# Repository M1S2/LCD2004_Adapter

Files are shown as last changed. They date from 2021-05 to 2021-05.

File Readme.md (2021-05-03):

# LCD2004 Adapter

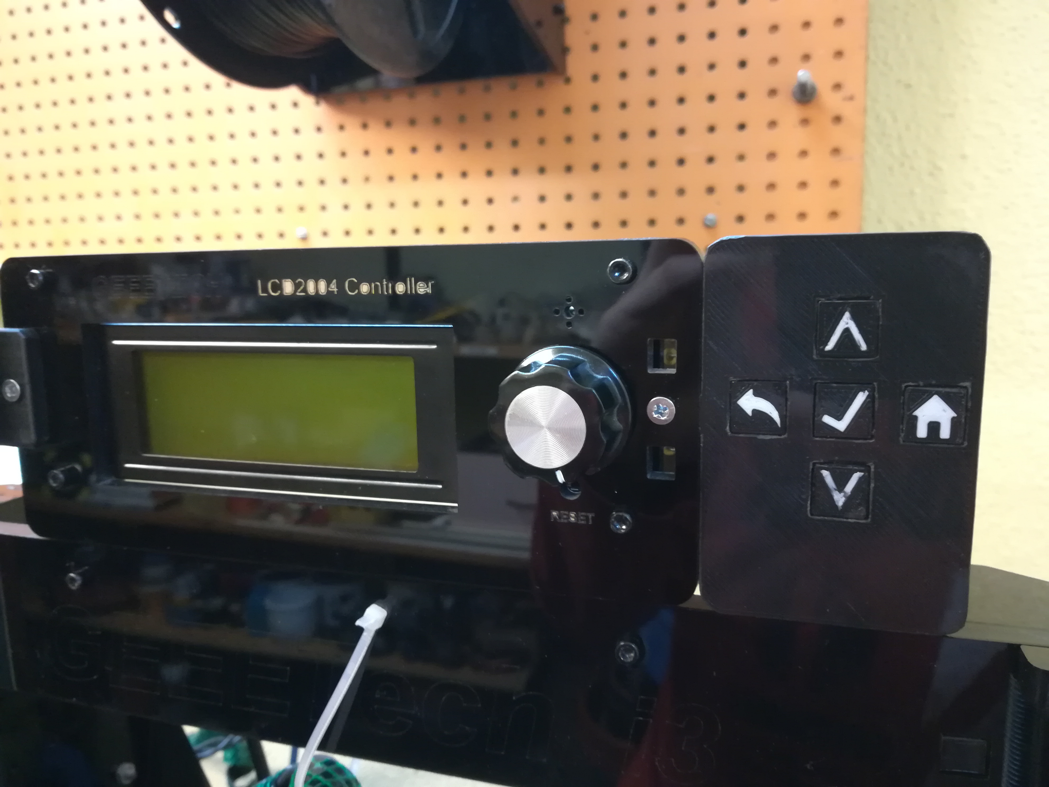
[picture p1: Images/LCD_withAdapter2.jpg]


This is an adapter to connect the DZ2004A-V1.0 LCD (Geeetech Prusa i3 pro B display) to the BIGTREETECH SKR E3 DIP V1.1 main board (LCD port).
This adapter is necessary because:
- The wiring of the LCD connectors on the display and the main board are different. The LCD2004 adapter connects the correct traces to make the display work again.
- The encoder isn't used anymore. The LCD2004 adapter is adding 5 push buttons as replacement for the encoder. The principle is inspired by the Zonestar LCD. 

Limitations:
- The encoder is out of service. This isn't a big deal, because it wasn't used that often because Octoprint is used most of the time to control the printer. So the 5 button keypad seemed to be good enough. Refer to section "Using the encoder again" of this Readme for some links how the encoder can maybe be used again.

## Principle of the 5 button keypad
The LCD2004 adapter is using 5 buttons to control the printers functions. This is inspired by the Zonestar display. 
Depending on which button is pressed, a different voltage is generated at the ADC_KEYPAD pin. This pin is read by an ADC on the main board.
The "UP" button is located on the bottom side of the PCB. This is correct because up means scrolling up which is the button on the bottom.

**Caution:** The SKR E3 DIP main board (and many other 32-bit boards) are working on 3.3V logic. Most pins on the ARM Cortex M3 STM32F103RCT6 are 5V tolerant (you can connect 5V to them) **but the ADC pin isn't (don't connect 5V to it)**! The LCD2004_Adapter uses a 3.3V zener diode to produce the correct voltage.

## PCB
The schematic and PCB was created using EAGLE. It was designed to be manufactured using toner transfer method so all traces are as big as possible.

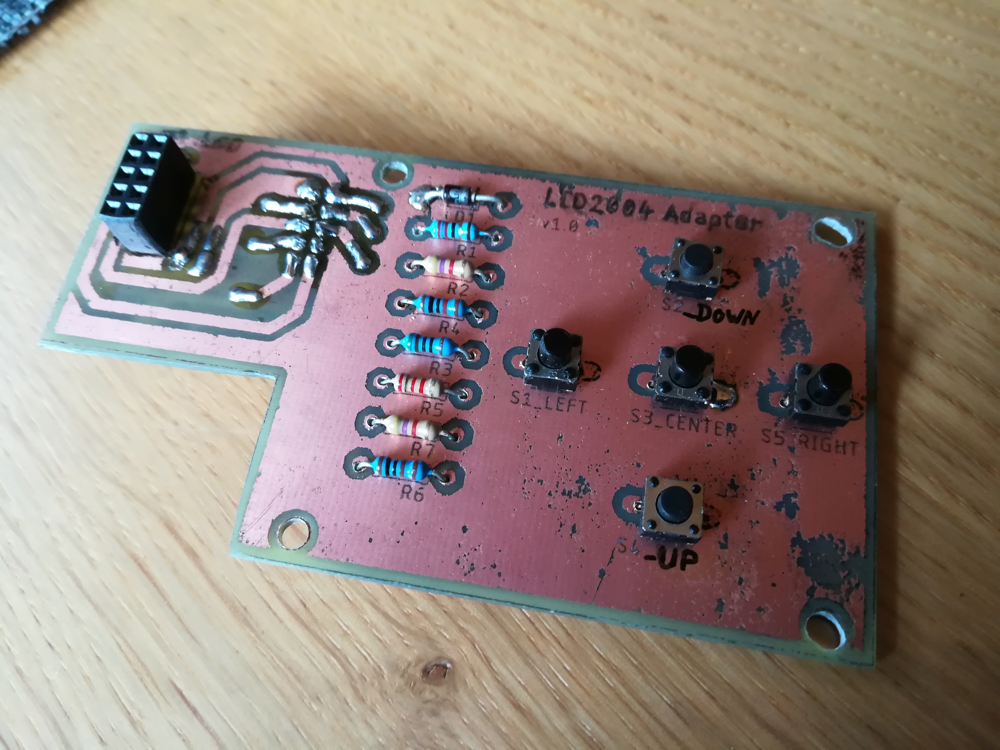
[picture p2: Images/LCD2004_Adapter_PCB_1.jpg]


## Housing
Print the following parts:
- 1x Keys_Housing.stl
- 1x Key_Back.stl and Key_Back_Icon.stl in one part
- 1x Key_Enter.stl and Key_Enter_Icon.stl in one part
- 1x Key_Home.stl and Key_Home_Icon.stl in one part
- 2x Key_Up_Down.stl and Key_Up_Down_Icon.stl in one part

**Caution:** The back, enter and home buttons are each 2 mm shorter because 2mm longer buttons were used here. The up and down buttons have the "correct" length.

The following parts are needed additionally:
- 2x 12mm spacers
- 1x M3 screw 10mm & M3 nut
- 2x wood screws 10mm

## Cabling
A default 10-pin ribbon cable can be used to connect the adapter with the main board. 
The only thing that must be changed here is to extract pin 8 (ADC_KEYPAD) on the main board side of the cable and wire it to the Servo pin (PA1) on the SKR E3 DIP board.

Cable complete                                |  SKR E3 DIP side
:--------------------------------------------:|:-------------------------:
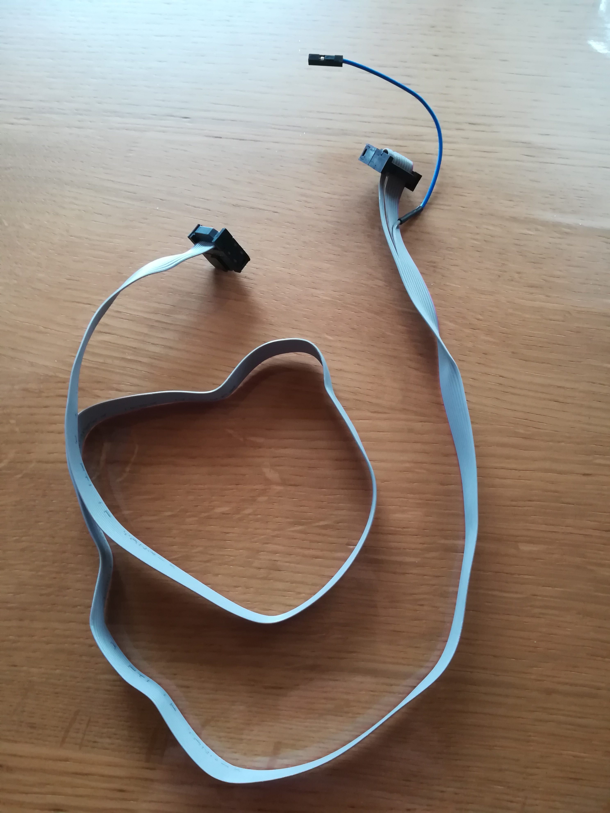
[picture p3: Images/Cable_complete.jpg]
Cable complete
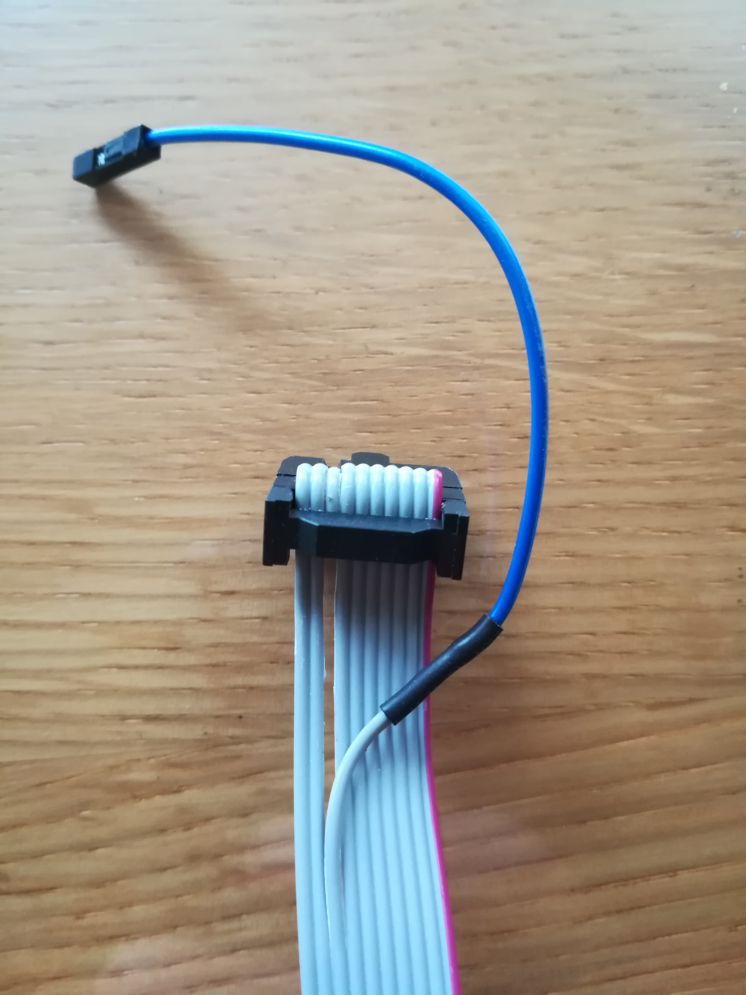
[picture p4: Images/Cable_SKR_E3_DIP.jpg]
Cable SKR E3 DIP side
 |  

## Firmware adaptions
Make the following adaptions to the Marlin firmware (line numbers are refering to Marlin 2.0.8):
- <Marlin root>/Marlin/Configuration.h: 
  Uncomment the `#define ZONESTAR_LCD` (in line 2086)
- <Marlin root>/Marlin/src/pins/stm32f1/pins_BTT_SKR_E3_DIP.h:
  Comment the line 190: `#error "CAUTION! ZONESTAR_LCD requires wiring modifications. See 'pins_BTT_SKR_MINI_E3_common.h' for details. Comment out this line to continue."`

## More Images
More images can be found in the [Images](/Images/) folder.

## Using the encoder again
To use the encoder again instead of the 5 buttons, here are some inspirations. Because Octoprint is used most of the time, there wasn't spent much time on this.

https://electronics.stackexchange.com/questions/231803/rotary-encoder-to-2-buttons

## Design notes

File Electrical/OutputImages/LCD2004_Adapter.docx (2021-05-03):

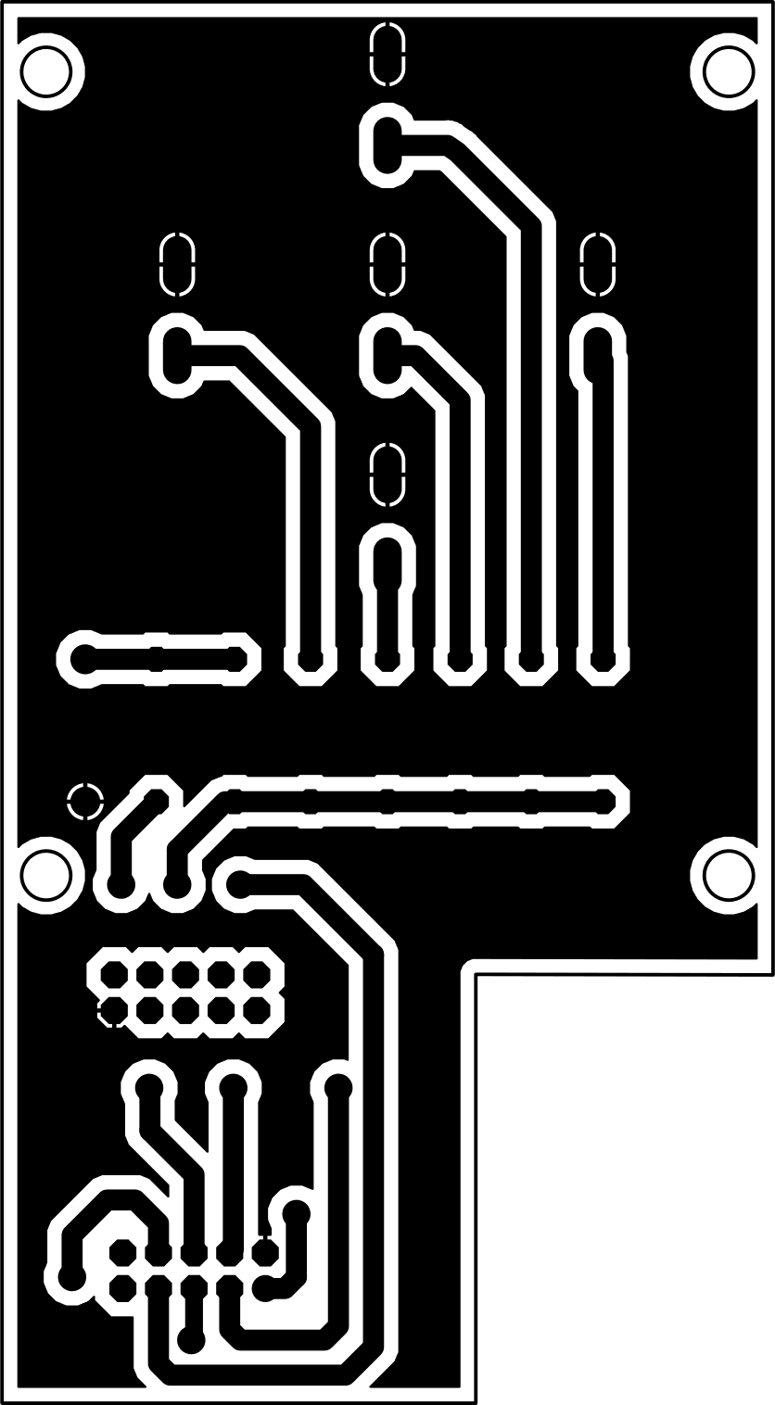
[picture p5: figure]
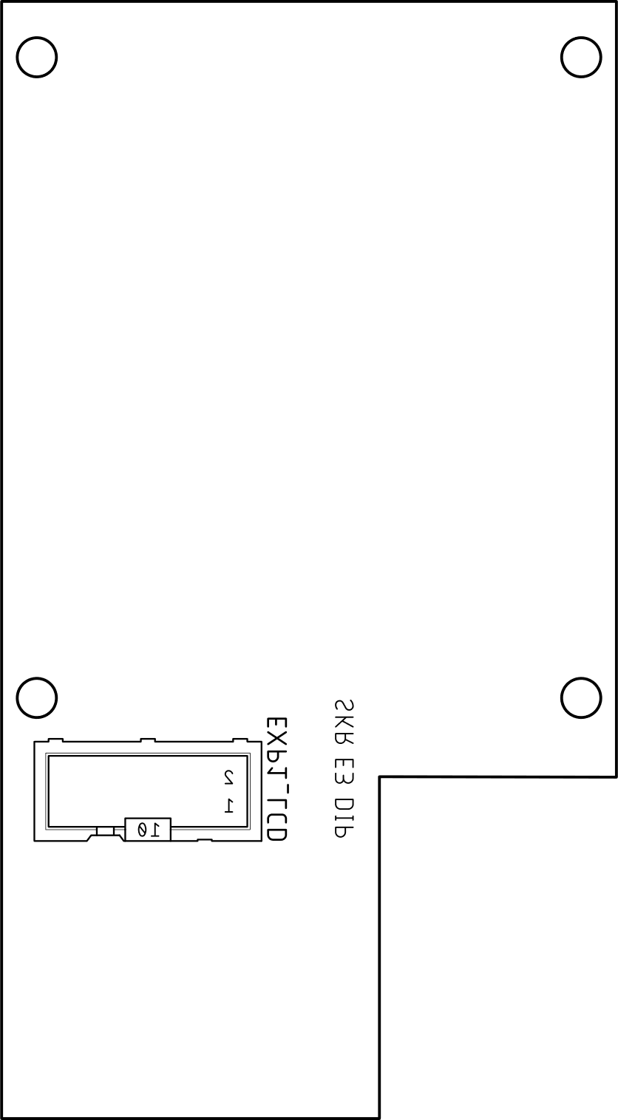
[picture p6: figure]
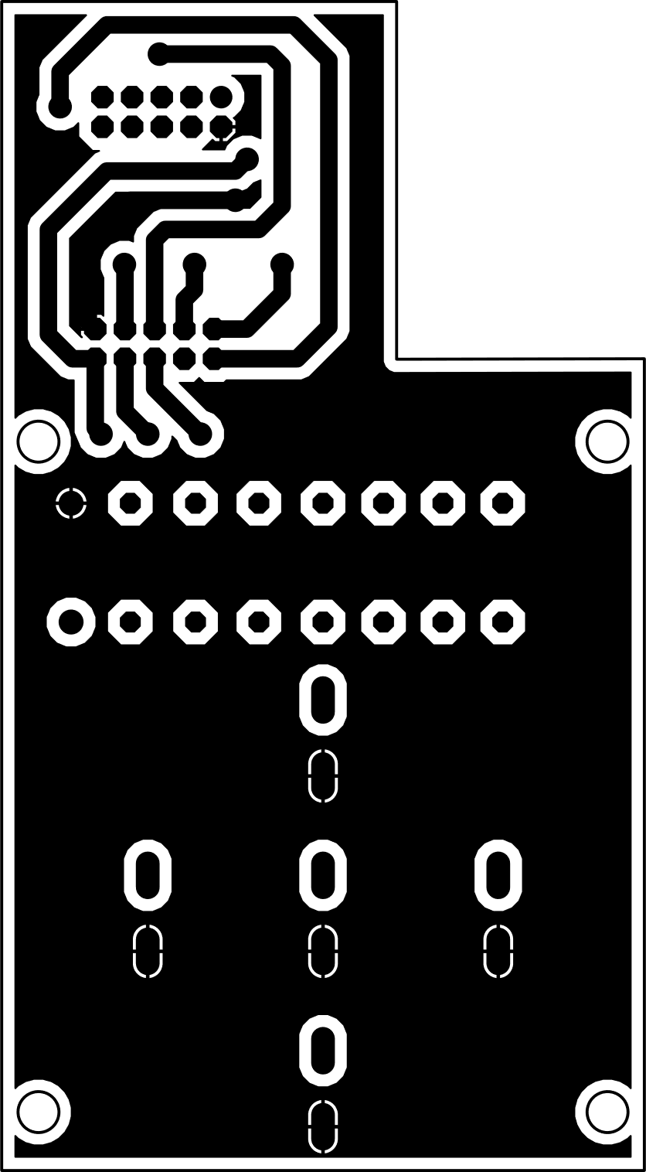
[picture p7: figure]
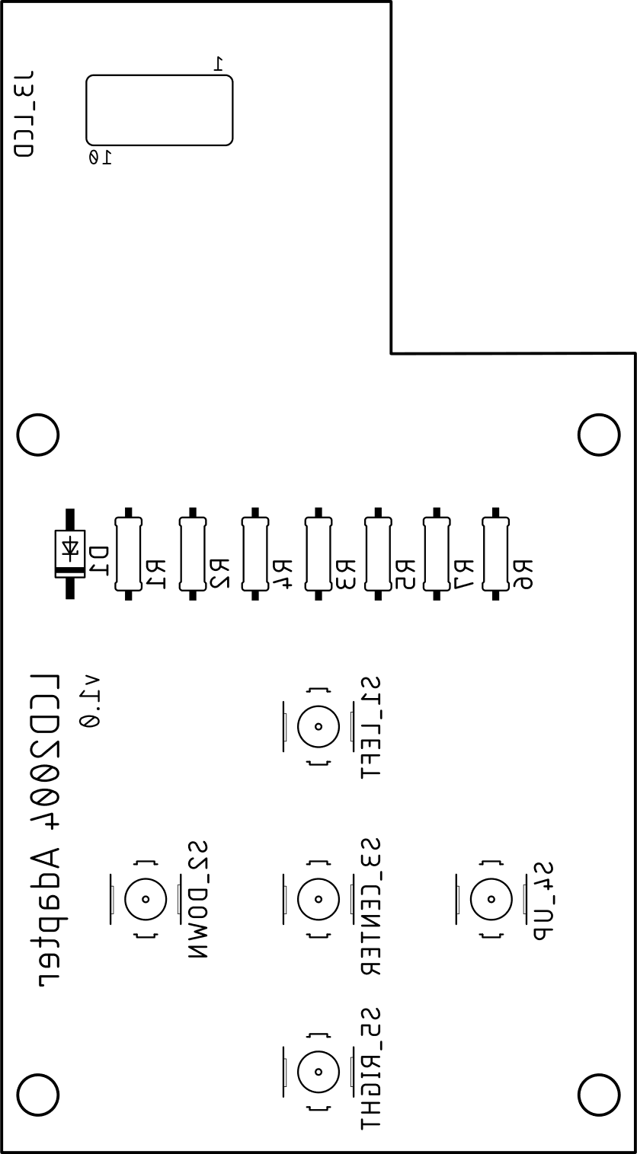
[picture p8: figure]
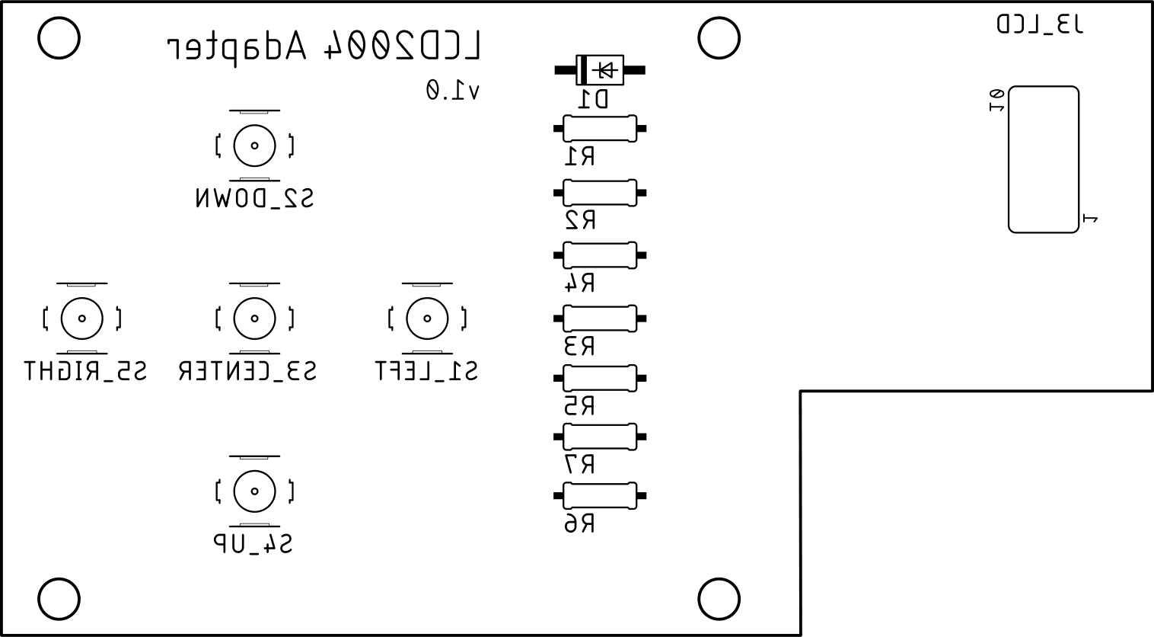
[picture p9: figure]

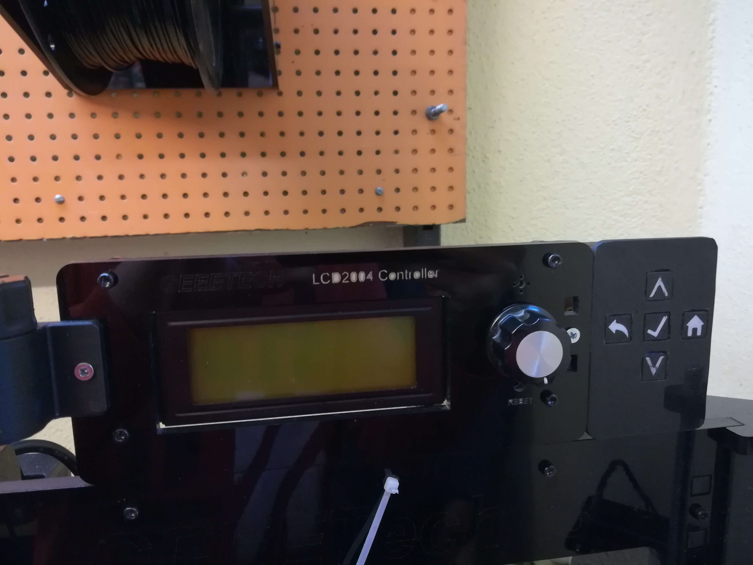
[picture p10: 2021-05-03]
Images/LCD_withAdapter1.jpg

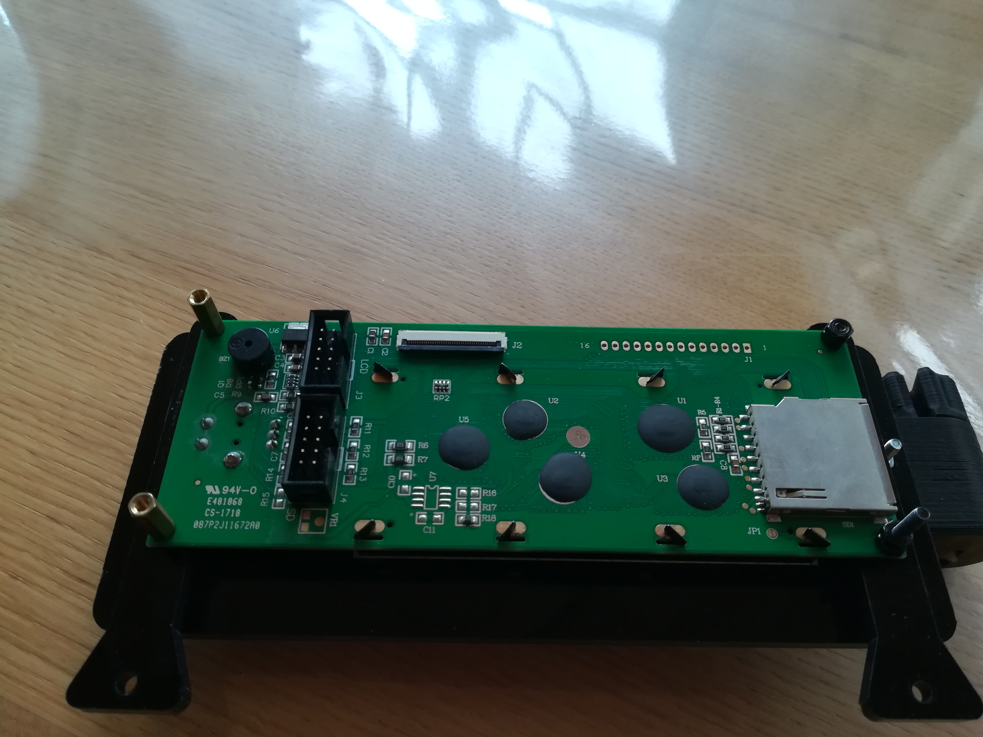
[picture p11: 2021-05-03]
Images/LCD_Back.jpg

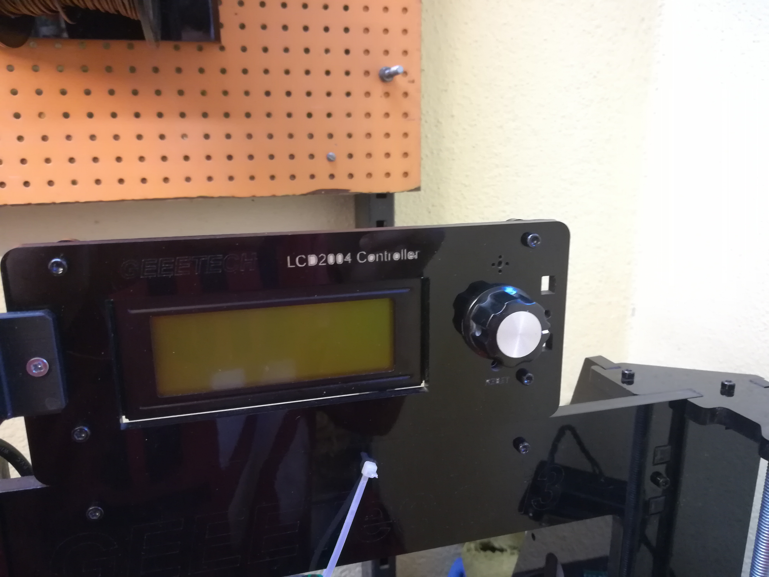
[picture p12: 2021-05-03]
Images/LCD_Before2.jpg

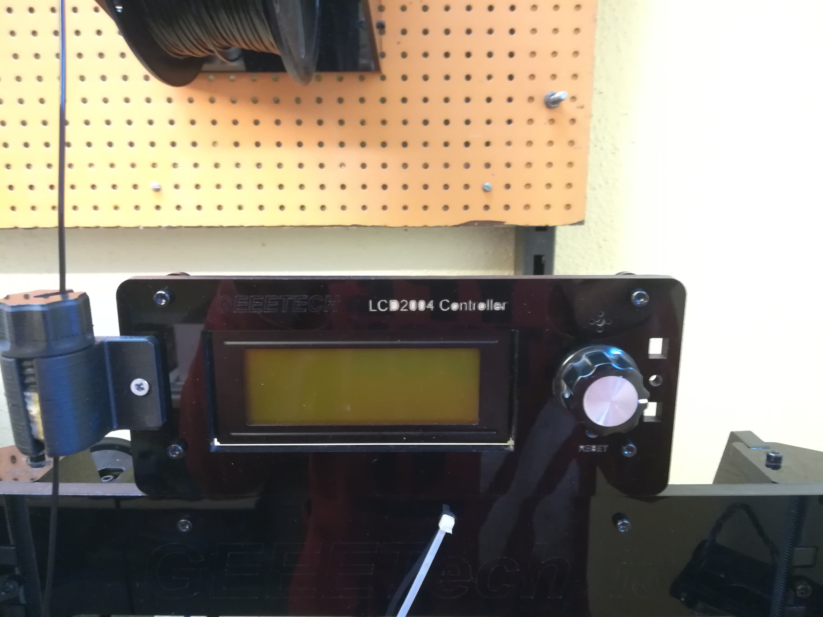
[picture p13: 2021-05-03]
Images/LCD_Before1.jpg

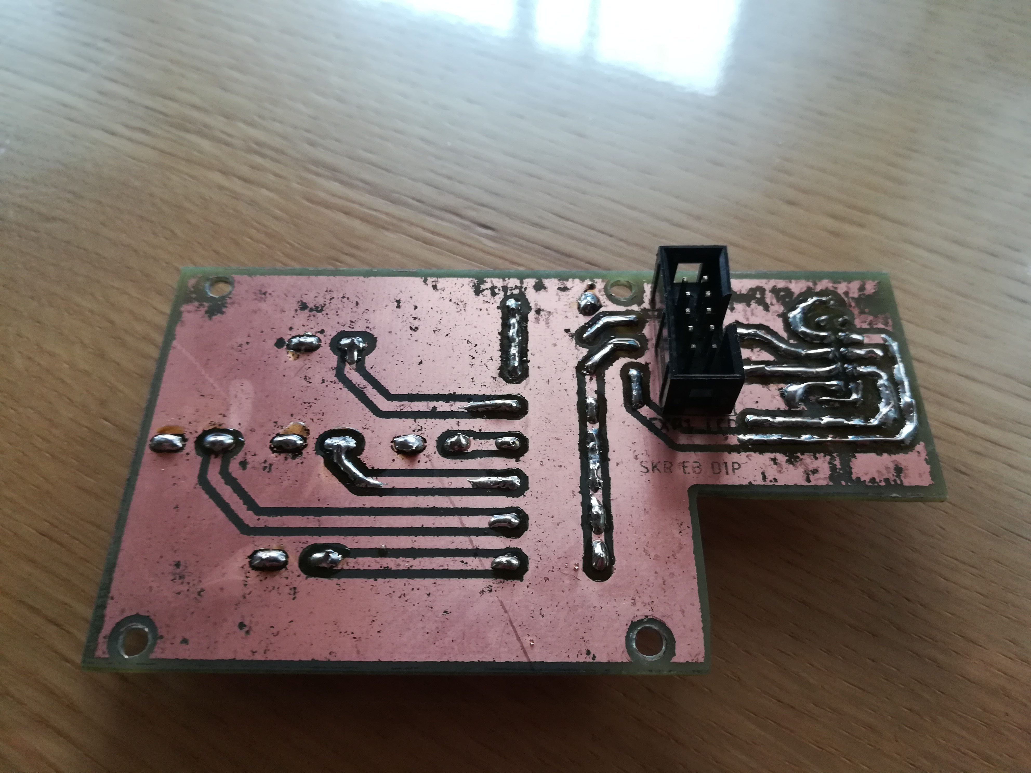
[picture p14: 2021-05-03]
Images/LCD2004_Adapter_PCB_2.jpg

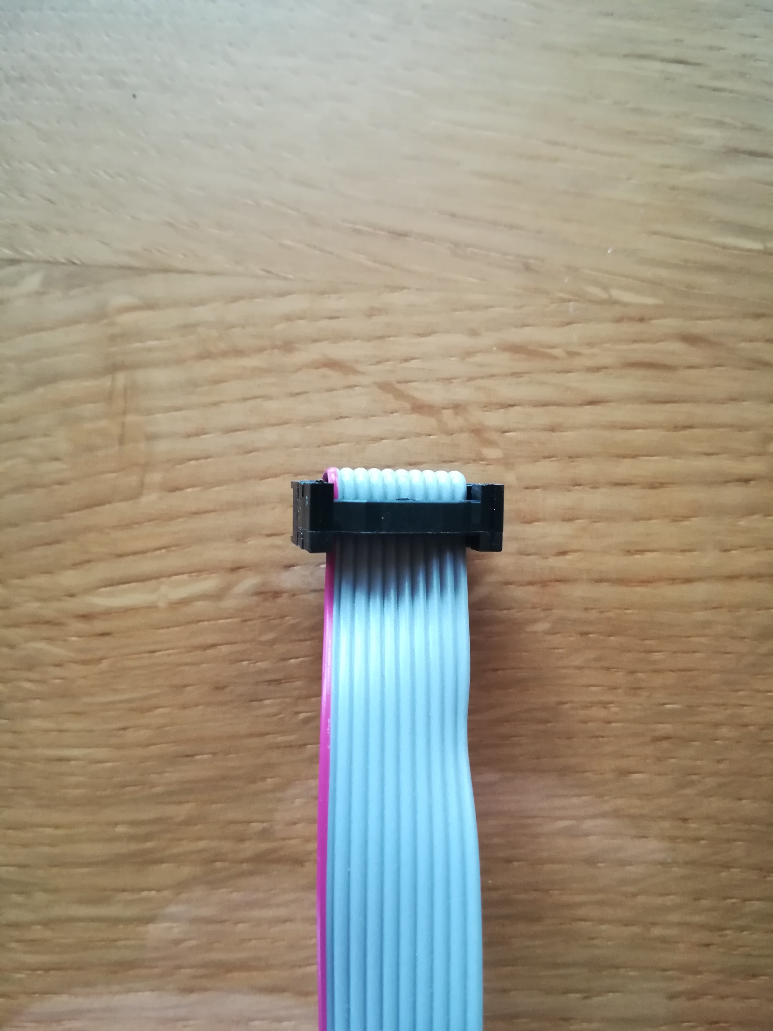
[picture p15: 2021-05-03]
Images/Cable_LCD2004_Adapter.jpg

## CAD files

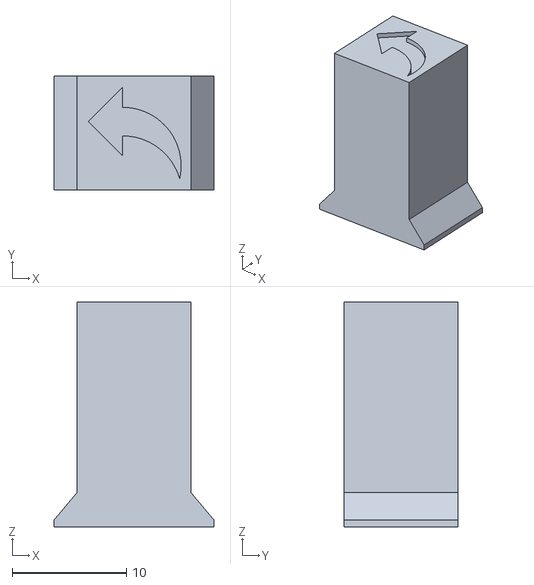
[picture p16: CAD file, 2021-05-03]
Mechanical/Key_Back.stl
14.0 x 10.0 x 19.7

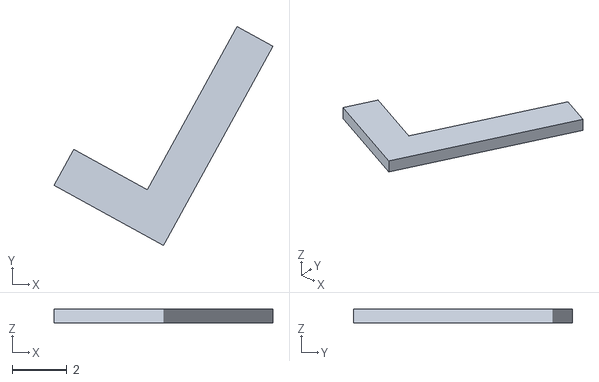
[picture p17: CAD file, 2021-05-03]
Mechanical/Key_Enter_Icon.stl
8.00 x 8.00 x 0.5

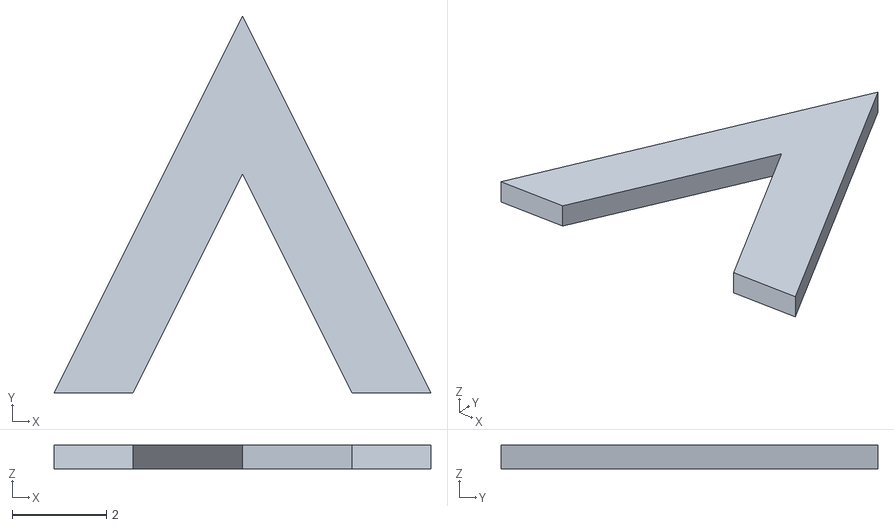
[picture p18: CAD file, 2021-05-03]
Mechanical/Key_Up_Down_Icon.stl
8.00 x 8.00 x 0.5

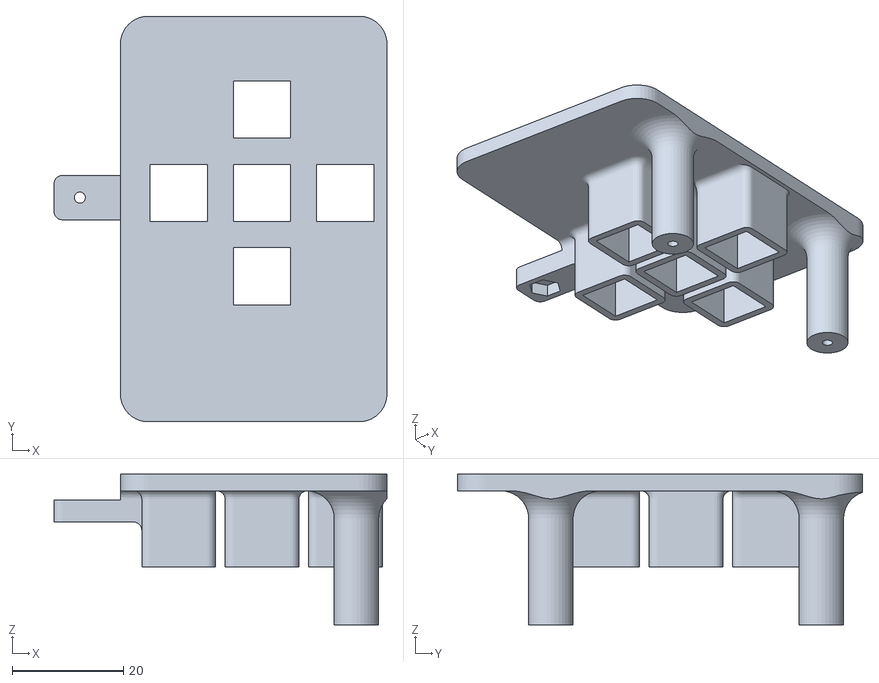
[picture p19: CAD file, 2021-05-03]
Mechanical/Keys_Housing.stl
60.0 x 73.0 x 27.1

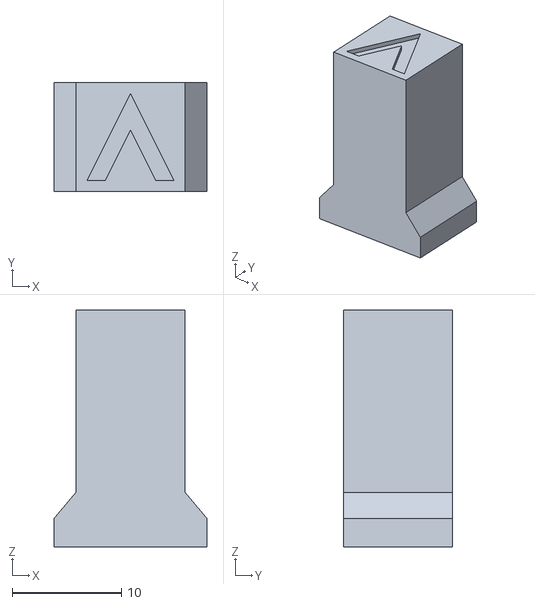
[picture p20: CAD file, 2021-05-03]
Mechanical/Key_Up_Down.stl
14.0 x 10.0 x 21.7

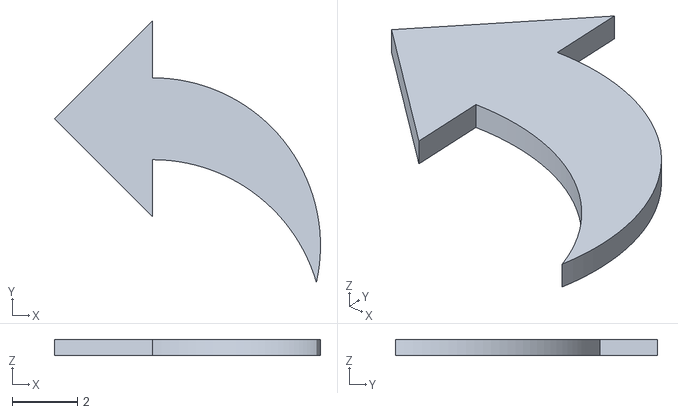
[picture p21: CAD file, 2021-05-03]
Mechanical/Key_Back_Icon.stl
8.12 x 8.00 x 0.5

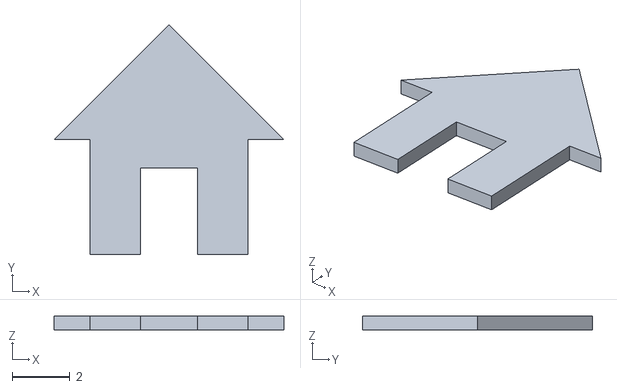
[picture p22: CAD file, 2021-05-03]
Mechanical/Key_Home_Icon.stl
8.00 x 8.00 x 0.5

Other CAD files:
Mechanical/Key_Enter.stl
Mechanical/Key_Home.stl
Mechanical/Assembly.f3z
Mechanical/Key_Back.f3d
Mechanical/Key_Enter.f3d
Mechanical/Key_Home.f3d
Mechanical/Key_Up_Down.f3d
Mechanical/Keys_Housing.f3d

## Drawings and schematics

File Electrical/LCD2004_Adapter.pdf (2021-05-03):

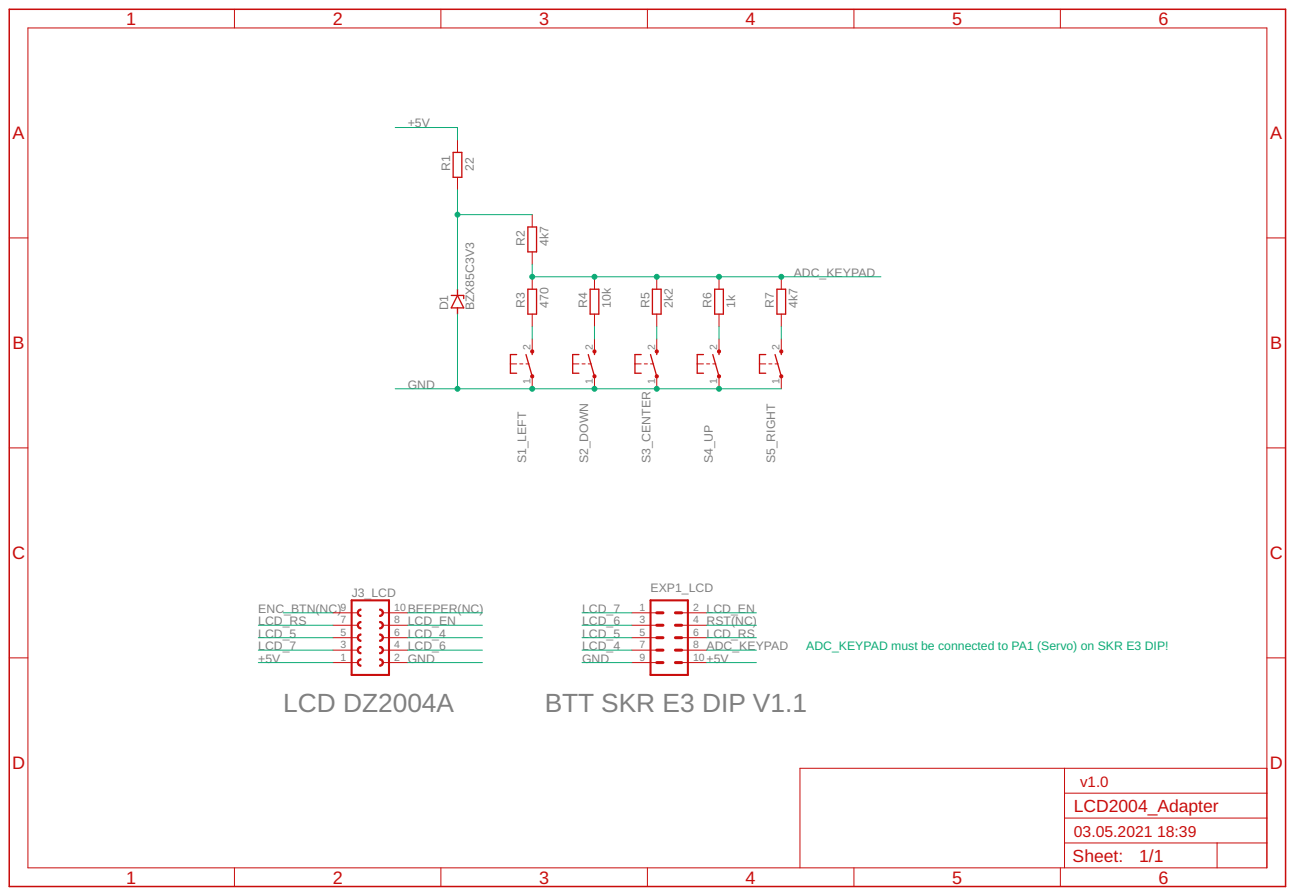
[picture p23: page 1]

ADC_KEYPAD must be connected to PA1 (Servo) on SKR E3 DIP!

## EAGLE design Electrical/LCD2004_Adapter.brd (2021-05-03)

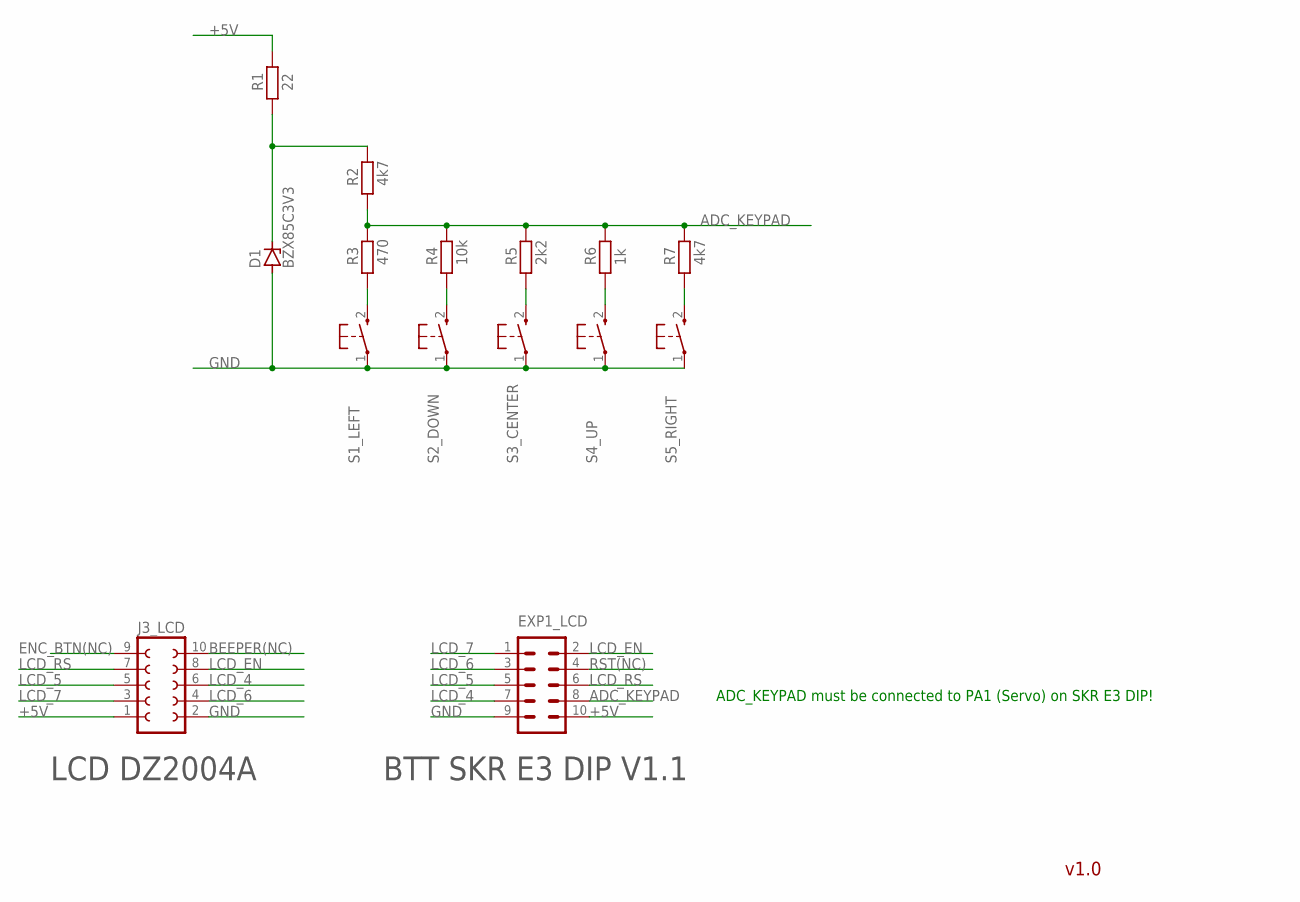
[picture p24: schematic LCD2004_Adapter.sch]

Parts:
D1: BZX85C3V3; DO41Z10
EXP1_LCD: ML10
J3_LCD: FE05-2
R1: 22; 0207/10
R2, R7: 4k7; 0207/10
R3: 470; 0207/10
R4: 10k; 0207/10
R5: 2k2; 0207/10
R6: 1k; 0207/10
S1_LEFT, S2_DOWN, S3_CENTER, S4_UP, S5_RIGHT: KURZHUBTASTER; B3F-10XX

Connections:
+5V: EXP1_LCD.10, J3_LCD.1, R1.2
ADC_KEYPAD: EXP1_LCD.8, R2.1, R3.2, R4.2, R5.2, R6.2, R7.2
BEEPER(NC): J3_LCD.10
ENC_BTN(NC): J3_LCD.9
GND: D1.A, EXP1_LCD.9, J3_LCD.2, S1_LEFT.1, S2_DOWN.1, S3_CENTER.1, S4_UP.1, S5_RIGHT.1
LCD_4: EXP1_LCD.7, J3_LCD.6
LCD_5: EXP1_LCD.5, J3_LCD.5
LCD_6: EXP1_LCD.3, J3_LCD.4
LCD_7: EXP1_LCD.1, J3_LCD.3
LCD_EN: EXP1_LCD.2, J3_LCD.8
LCD_RS: EXP1_LCD.6, J3_LCD.7
unnamed: D1.C, R1.1, R2.2
unnamed: R3.1, S1_LEFT.2 (S)
unnamed: R4.1, S2_DOWN.2 (S)
unnamed: R5.1, S3_CENTER.2 (S)
unnamed: R6.1, S4_UP.2 (S)
unnamed: R7.1, S5_RIGHT.2 (S)
RST(NC): EXP1_LCD.4

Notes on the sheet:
LCD DZ2004A
BTT SKR E3 DIP V1.1
ADC_KEYPAD must be connected to PA1 (Servo) on SKR E3 DIP!
v1.0

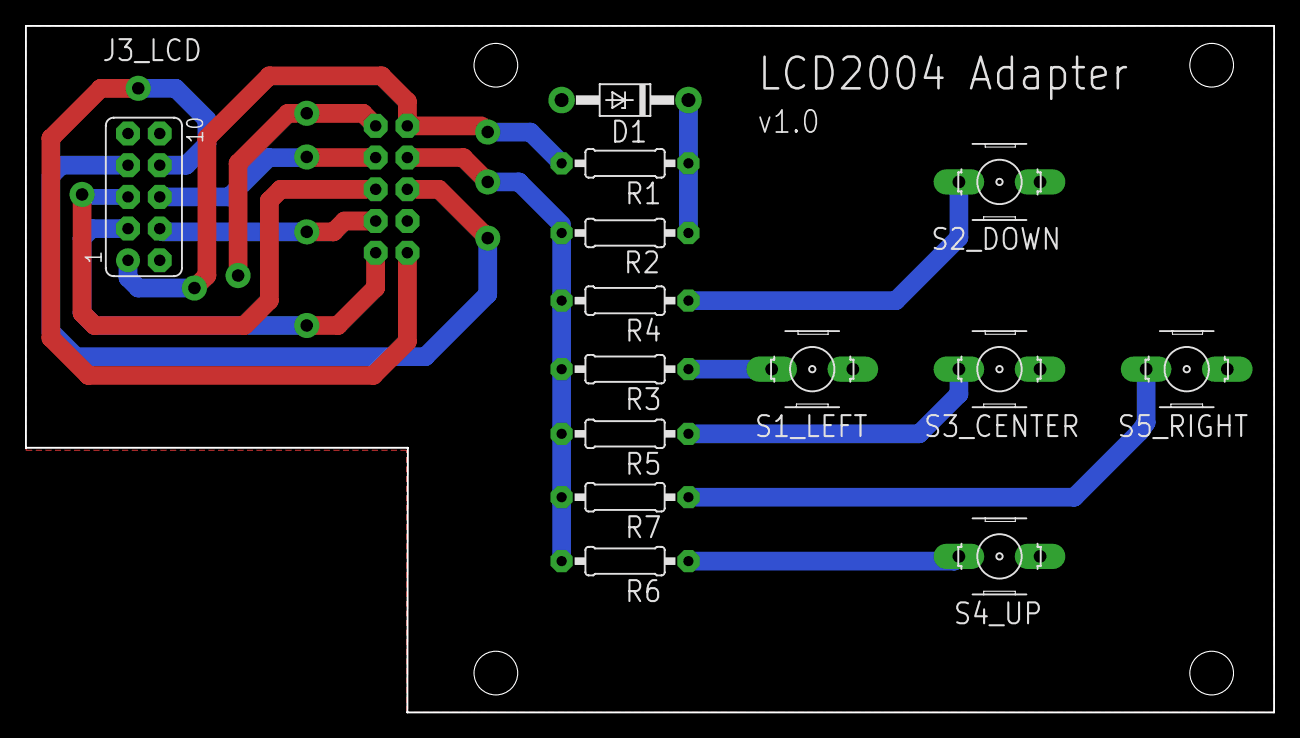
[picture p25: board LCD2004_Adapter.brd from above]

Board: 2 copper layers, 100.0 x 55.0 mm, 15 parts (1 on the bottom side), 15 nets.

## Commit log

2021-04-30 Initial commit containing all electrical files
    [LCD2004_Adapter.brd, LCD2004_Adapter.sch, LCD_DZ2004A-V1.3.stl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]
2021-05-03 Swapped Up and Down buttons on PCB (making equal to Zonestar LCD)
    [LCD2004_Adapter.brd, LCD2004_Adapter.sch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]
2021-05-03 Mechanical design added
    [Assembly.f3z, Key_Back.f3d, Key_Back.stl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]
